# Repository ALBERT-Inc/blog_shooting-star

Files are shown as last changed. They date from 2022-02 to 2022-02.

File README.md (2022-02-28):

# 流れ星に全自動で願いを送る装置を作る
ブログ記事、[流れ星に全自動で願いを送る装置を作る](https://blog.albert2005.co.jp/2022/02/28/shooting-star/)の実験で使用したプログラムです。

## 実行方法
- `requirements.txt` に書かれているライブラリをインストールしてください．
- その後、`src`に格納されている以下のプログラムを順番に実行してください。
    1. `calibration.py`
    2. `pre_capture.py`
    3. `make_MLP_model.py`
- ARマーカーの追跡実験をやる場合は`AR_marker_capture.py`を、流れ星の追跡実験をやる場合は`star_capture.py`を実行してください。

## 機材リスト
- カメラ：
  - 本体：OMRON SENTECH STC-MCS241U3V
  - レンズ：興和光学 LM6HC
- マイコン：Arduino Uno R3
- モーター関連：
  - ステッピングモーター：42mm ステッピングモータ 2.8V 2相 400ステップ
  - モータードライバー：L6470
  - マウント：5mm ユニバーサルマウント ※モーターの軸に鏡を取り付けるためのもの
- その他
  - ACアダプター：GF12-US1210
  - コネクター：2.1ｍｍ標準DCジャック⇔スクリュー端子台
  - 耐熱電子ワイヤー　2m x 7色　外径1.22mm (UL3265　AWG24) ※DCジャックとモータードライバーを接続
  - ミラー：カッターで切れる軽量安全ミラー 厚さ 2mm 幅 100mm、TMPEC-1015
  - ジャンパワイヤ

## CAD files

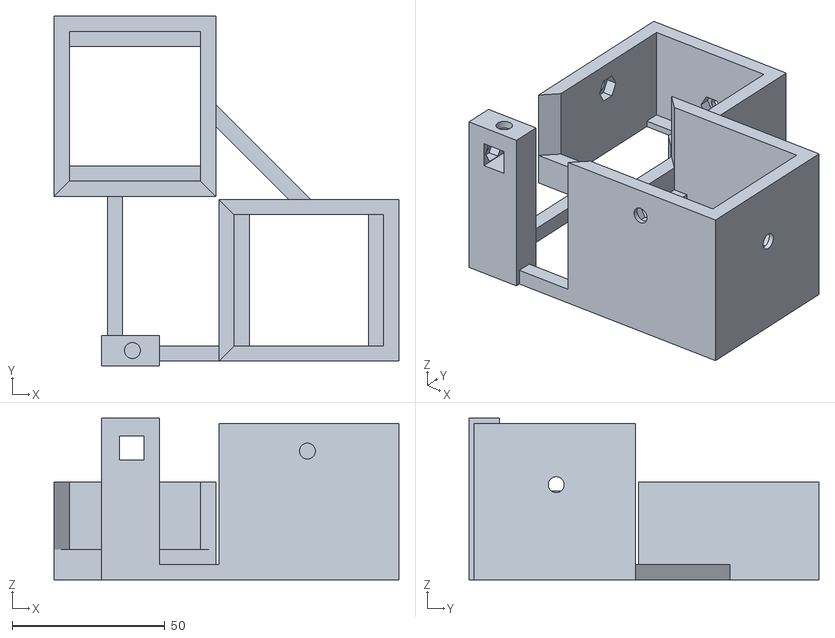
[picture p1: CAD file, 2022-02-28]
3D_model/base.stl
113.0 x 114.5 x 53.0

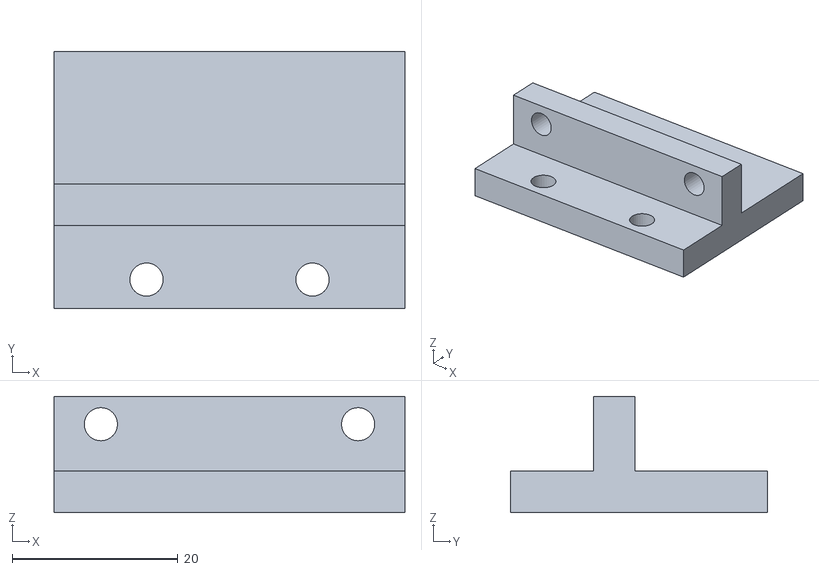
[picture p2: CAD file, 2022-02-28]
3D_model/cam_base.stl
42.3 x 31.0 x 14.0

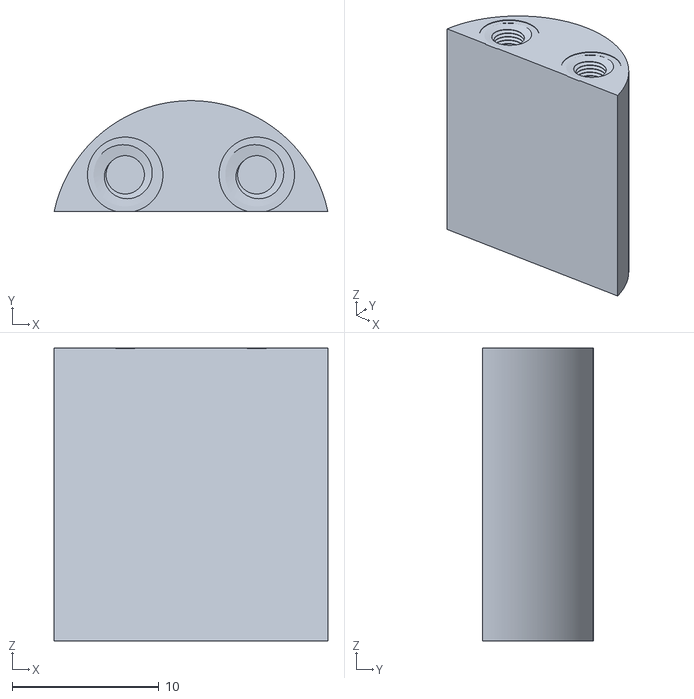
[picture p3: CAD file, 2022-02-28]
3D_model/mirror_base_nut.stl
18.7 x 7.55 x 20.0

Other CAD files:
3D_model/base.blend
3D_model/base_合成前.blend
3D_model/base_穴あけ合成前.blend
3D_model/cam_base.blend
3D_model/cam_base_穴あけ前.blend
3D_model/mirror_base_nut.blend

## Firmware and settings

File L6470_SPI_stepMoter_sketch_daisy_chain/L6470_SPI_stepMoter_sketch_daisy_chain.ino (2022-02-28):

/*デイジーチェン接続 
Arduino11番ピン（MOSI）- 6番ピン(SDI) L6470(一台目) 3番ピン(SDO) - (SDI)L6470(二台目)(SDO) - 12番ピン（MISO) Arduino
SCK 共通
SS - CS共通
*/
#include <SPI.h>
#include <stdio.h>

// ピン定義。
#define PIN_SPI_MOSI 11
#define PIN_SPI_MISO 12
#define PIN_SPI_SCK 13
#define PIN_SPI_SS 10
#define PIN_BUSY 9
#define PIN_BUSY2 8

void setup()
{
  pinMode(PIN_SPI_MOSI, OUTPUT);
  pinMode(PIN_SPI_MISO, INPUT);
  pinMode(PIN_SPI_SCK, OUTPUT);
  pinMode(PIN_SPI_SS, OUTPUT);
  pinMode(PIN_BUSY, INPUT_PULLUP);
  pinMode(PIN_BUSY2, INPUT_PULLUP);
  SPI.begin();
  SPI.setDataMode(SPI_MODE3);
  SPI.setBitOrder(MSBFIRST);
  Serial.begin(9600);
  digitalWrite(PIN_SPI_SS, HIGH);

  L6470_resetdevice(); //1台目のL6470リセット
  L6470_resetdevice2(); //2台目のL6470リセット
  L6470_setup();  //1台目のL6470を設定 
  L6470_setup2();  //2台目のL6470を設定 
  L6470_getstatus(); //1台目のフラグ解放
  L6470_getstatus2();//2台目のフラグ解放
}

void loop(){
  while (1) {
    String line;   // 受信文字列  
    String data_[4] = {"\0"};

    signed char c;
    //データが存在するときだけ受信処理以降を行う(頭の0が使われる)
    if((c = Serial.read()) != -1){
      line = Serial.readStringUntil('\n');
      char ind = 0;
      char len_ = line.length();
        
      for (char i = 0; i < len_; i++) {
        char tmp = line.charAt(i);
        if ( tmp == ',' ) {
          ind++;
        }
        else data_[ind] += tmp;
      }
  
      if (data_[0] == "remark") {
        L6470_setparam_mark(data_[1].toInt());
        L6470_setparam_mark2(data_[2].toInt());
      }
      else if (data_[0] == "reset"){
        L6470_gomark();
        L6470_gomark2();
      }
      else if (data_[0] == "home"){
        L6470_gohome();
        L6470_gohome2();
      }
      
      else {
        //回転方向,step数
        L6470_move(data_[0].toInt(),data_[1].toInt());//指定方向に連続回転
        L6470_move2(data_[2].toInt(),data_[3].toInt());//指定方向に連続回転
        L6470_busydelay(0); //命令を受け付けるまで待機
        L6470_busydelay2(0); //命令を受け付けるまで待機
        Serial.println("d");        
      }
    }
  }
}

void L6470_setup(){
L6470_setparam_acc(3000); //[R, WS] 加速度default 0x08A (12bit) (14.55*val+14.55[step/s^2])
L6470_setparam_dec(3000); //[R, WS] 減速度default 0x08A (12bit) (14.55*val+14.55[step/s^2])
L6470_setparam_maxspeed(90); //[R, WR]最大速度default 0x041 (10bit) (15.25*val+15.25[step/s])
L6470_setparam_minspeed(0x1200); //[R, WS]最小速度default 0x000 (1+12bit) (0.238*val[step/s])
L6470_setparam_fsspd(0x027); //[R, WR]μステップからフルステップへの切替点速度default 0x027 (10bit) (15.25*val+7.63[step/s])
L6470_setparam_kvalhold(0x28); //[R, WR]停止時励磁電圧default 0x29 (8bit) (Vs[V]*val/256)
L6470_setparam_kvalrun(0x28); //[R, WR]定速回転時励磁電圧default 0x29 (8bit) (Vs[V]*val/256)
L6470_setparam_kvalacc(0x28); //[R, WR]加速時励磁電圧default 0x29 (8bit) (Vs[V]*val/256)
L6470_setparam_kvaldec(0x28); //[R, WR]減速時励磁電圧default 0x29 (8bit) (Vs[V]*val/256)

L6470_setparam_stepmood(6); //ステップモードdefault 0x07 (1+3+1+3bit)
}

void L6470_setup2(){
L6470_setparam_acc2(3000); //[R, WS] 加速度default 0x08A (12bit) (14.55*val+14.55[step/s^2])
L6470_setparam_dec2(3000); //[R, WS] 減速度default 0x08A (12bit) (14.55*val+14.55[step/s^2])
L6470_setparam_maxspeed2(90); //[R, WR]最大速度default 0x041 (10bit) (15.25*val+15.25[step/s])
L6470_setparam_minspeed2(0x1200); //[R, WS]最小速度default 0x000 (1+12bit) (0.238*val[step/s])
L6470_setparam_fsspd2(0x027); //[R, WR]μステップからフルステップへの切替点速度default 0x027 (10bit) (15.25*val+7.63[step/s])
L6470_setparam_kvalhold2(0x28); //[R, WR]停止時励磁電圧default 0x29 (8bit) (Vs[V]*val/256)
L6470_setparam_kvalrun2(0x28); //[R, WR]定速回転時励磁電圧default 0x29 (8bit) (Vs[V]*val/256)
L6470_setparam_kvalacc2(0x28); //[R, WR]加速時励磁電圧default 0x29 (8bit) (Vs[V]*val/256)
L6470_setparam_kvaldec2(0x28); //[R, WR]減速時励磁電圧default 0x29 (8bit) (Vs[V]*val/256)

L6470_setparam_stepmood2(6); //ステップモードdefault 0x07 (1+3+1+3bit)
}


void fulash(){
  long a=L6470_getparam_abspos();
  long b=L6470_getparam_speed();
  long c=L6470_getparam_abspos2();
  long d=L6470_getparam_speed2();
  char str[15];
  snprintf(str,sizeof(str),"1pos=0x%6.6X ",a);
  snprintf(str,sizeof(str),"1spd=0x%5.5X ",b);
  snprintf(str,sizeof(str),"2pos=0x%6.6X ",c);
  snprintf(str,sizeof(str),"2spd=0x%5.5X ",d);
}

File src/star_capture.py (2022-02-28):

import serial
import time
import math
import multiprocessing
import ctypes
import collections
import pickle
import cv2
from cv2 import aruco
import numpy as np
import torch
import torch.nn as nn
from harvesters.core import Harvester

from model import DestStep
from util import step2order

model_name = "./data/model.pth"
# カメラ撮影画像表示の場合はTrue(処理は遅くなる)
capture_image = False
calibration = True

camera_width = 1280
camera_height = 720
resize_x = 640
resize_y = 360
no_ar_max_cnt = 60

# 2回目にレーザー光が反射する高さ(m)
output_height = 0.0192
# モーター1周のstep数
motor_step = 25600

ser = serial.Serial('/dev/cu.usbmodem14101', 9600)

marker_length = 0.059  # [m]
aruco = cv2.aruco  # arucoライブラリ
dictionary = aruco.getPredefinedDictionary(aruco.DICT_4X4_50)
camera_matrix = np.load("./data/mtx.npy")
distortion_coeff = np.load("./data/dist.npy")


# カメラから取得したcomponentを画像に変換する
def capture_process(img_queue, capture_count):
    # カメラの設定
    h = Harvester()
    h.add_file('/Library/Frameworks/SentechSDK.framework/Libraries/libstgentl.cti')
    h.update()
    ia = h.create_image_acquirer(0)
    ia.remote_device.node_map.UserSetSelector.value = 'Default'
    ia.remote_device.node_map.ExposureAuto = 'Off'
    ia.remote_device.node_map.ExposureMode = 'Timed'
    ia.remote_device.node_map.TriggerSelector.value = 'FrameStart'
    ia.remote_device.node_map.TriggerMode.value = 'On'
    ia.remote_device.node_map.TriggerSource.value = 'Line0'
    ia.remote_device.node_map.Width.value = camera_width
    ia.remote_device.node_map.Height.value = camera_height
    # デジタルゲイン、ホワイトバランスゲイン(カラーのみ)
    ia.remote_device.node_map.Gain.value = 239.0
    print(ia.remote_device.node_map.PixelFormat.value)
    ia.start_acquisition()
    
    while True:
        with ia.fetch_buffer() as buffer:
            component = buffer.payload.components[0].data
            image = component.reshape(camera_height, camera_width)
            img = cv2.cvtColor(image, cv2.COLOR_BAYER_RG2RGB)
            # ctypes配列に変換
            np.ctypeslib.as_array(img_queue.get_obj())[:] = img
            capture_count.value += 1


def calc_process(i, img_queue, calc_count,
                 ar_marker_pos_x, ar_marker_pos_y,
                 ar_marker_pos_z, no_ar_cnt, calibration_flag):
    pre_img = np.zeros((resize_y, resize_x, 3))
    while True:
        calc_count.value += 1
        img = np.ctypeslib.as_array(img_queue.get_obj())
        img_small = cv2.resize(img, (resize_x, resize_y))
        img_small = img_small.astype(np.int16)
        diff_img = np.clip((img_small - pre_img), 0, 255)
        #print("all", np.max(np.sum(diff_img, axis=2).flatten()))
        #print(np.max(diff_img[:, :,0].flatten()), np.max(diff_img[:, :,1].flatten()), np.max(diff_img[:, :,2].flatten()))
        pointer = np.where((np.sum(diff_img, axis=2) > 90) * (diff_img[:, :, 2] < 80))
        #pointer = np.where((np.sum(diff_img, axis=2) > 150))
        pre_img = img_small
        if (calibration_flag.value) or (len(pointer[0]) > 0):
            if calibration_flag.value == 1:
                corners, ids, rejectedImgPoints = aruco.detectMarkers(img, dictionary)
                if len(corners) == 0:
                    continue
                no_ar_cnt.value = 0
                # マーカーの半分のサイズ[pixel]
                m_size = ((corners[0][0][1][0] - corners[0][0][0][0])
                          + (corners[0][0][2][1] - corners[0][0][1][1])) / 4

            elif len(pointer[0]) > 0:
                no_ar_cnt.value = 0
                #print(time.time())
                pointer_x = np.mean(pointer[1]) * (camera_width / resize_x)
                pointer_y = np.mean(pointer[0]) * (camera_height / resize_y)
                corners = np.array([[[[pointer_x-m_size, pointer_y+m_size],
                                      [pointer_x+m_size, pointer_y+m_size],
                                      [pointer_x+m_size, pointer_y-m_size],
                                      [pointer_x-m_size, pointer_y-m_size]]]])
            
            rvec, tvec, each_corner = aruco.estimatePoseSingleMarkers(corners[0], marker_length,
                                                            camera_matrix, distortion_coeff)
            tvec = np.squeeze(tvec + each_corner[0])
            # Y軸方向だけ上下が逆になっている
            ar_marker_pos_x.value = round(tvec[0], 4)
            ar_marker_pos_y.value = -round(tvec[1], 4)
            ar_marker_pos_z.value = round(tvec[2], 4)
        else:
            no_ar_cnt.value += 1


def main():
    # マルチプロセス数
    # macbook airだとmultiprocessing.cpu_count() = 4
    process_num = 2
    #process_num = multiprocessing.cpu_count()
    print("process_num: ", process_num)

    # 処理した画像データを入れるキュー (ctypes配列)
    img_queue = multiprocessing.Value(
        ((ctypes.c_uint8 * 3) * camera_width) * camera_height)
    # 処理した画像の枚数を数える
    capture_count = multiprocessing.Value('i', 0)
    calc_count = multiprocessing.Value('i', 0)
    # ARマーカーの座標
    ar_marker_pos_x = multiprocessing.Value('f', -1)
    ar_marker_pos_y = multiprocessing.Value('f', -1)
    ar_marker_pos_z = multiprocessing.Value('f', -1)
    no_ar_cnt = multiprocessing.Value('i', 1)
    calibration_flag = multiprocessing.Value('i', 1)

    # プロセス生成
    process_set = []
    # 撮影プロセス
    process_ = multiprocessing.Process(
        target=capture_process,
        args=(img_queue, capture_count))
    process_.start()
    process_set.append(process_)

    # 計算プロセス (ARマーカー検出)
    for i in range(process_num - 1):
        process_ = multiprocessing.Process(
            target=calc_process,
            args=(i, img_queue, calc_count,
                  ar_marker_pos_x, ar_marker_pos_y,
                  ar_marker_pos_z, no_ar_cnt, calibration_flag))
        process_.start()
        process_set.append(process_)

    # MLP
    model = DestStep(output_height, motor_step)
    model.load_state_dict(torch.load(model_name))

    # Arduinoの初期設定を待つ
    time.sleep(2)

    main_count = 0
    # 命令前のモーターのstep数
    pre_step_x = 0
    pre_step_y = 0
    calibration_flag.value = calibration
    start_time = time.time()

    # Cntl + c でexceptへ
    try:
        while True:
            if capture_image:
                # ctypes配列をnumpy配列に変換
                img = np.ctypeslib.as_array(img_queue.get_obj())
                # ARマーカー検出&描画
                corners, ids, rejectedImgPoints = aruco.detectMarkers(
                    img, dictionary)
                aruco.drawDetectedMarkers(img, corners, ids, (0, 255, 255))
                # 画像を描画
                cv2.imshow('drawDetectedMarkers', img)
                if cv2.waitKey(1) & 0xFF == ord('q'):
                    break
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
